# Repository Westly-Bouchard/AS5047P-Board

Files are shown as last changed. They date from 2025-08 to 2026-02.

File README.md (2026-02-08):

  Big thanks to [PCBWay](https://www.pcbway.com/) for sponsoring this project! Their support enables me (and hundreds of other designers) to make cool stuff. More info in [Manufacturing](#manufacturing)
<div align="center">
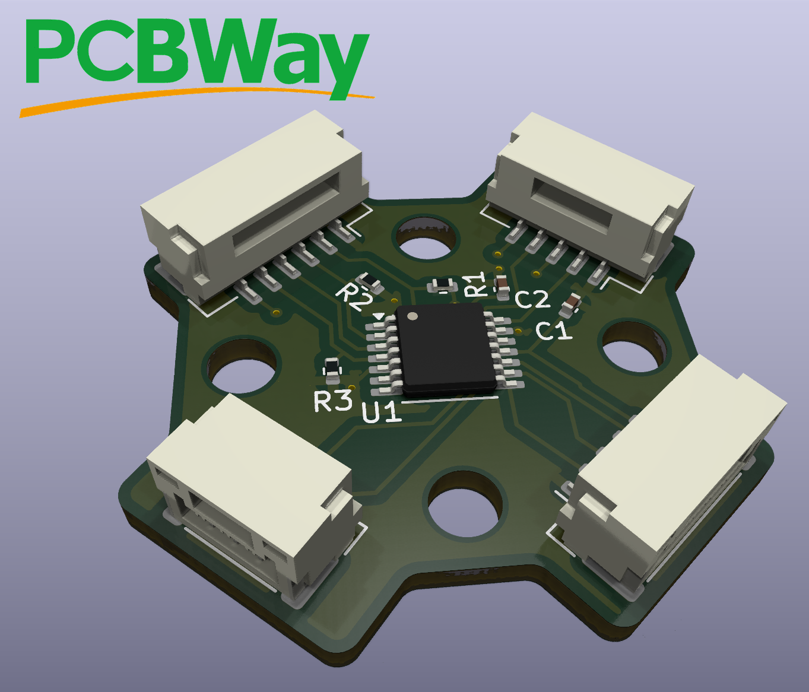
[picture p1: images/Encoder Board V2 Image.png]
  
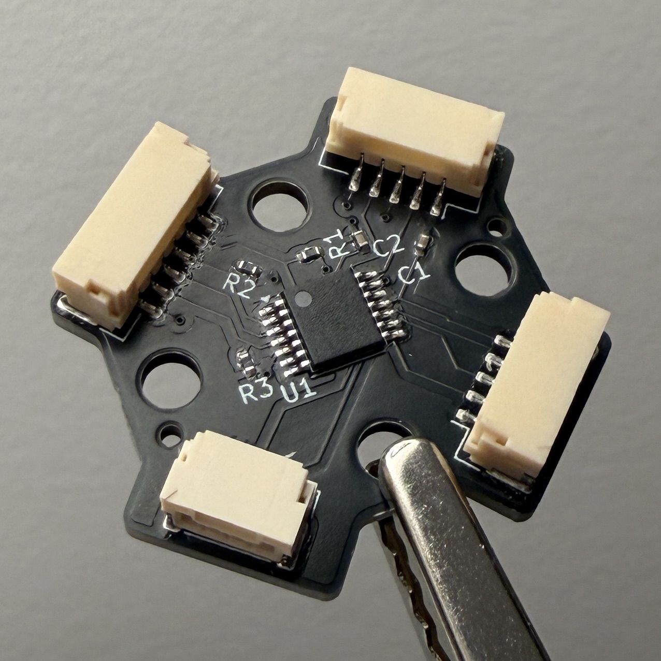
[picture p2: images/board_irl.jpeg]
  
</div>
<br>
<p>
This is a breakout pcb for the commonly used AS5047P magnetic position sensor IC. Its SPI communication protocols are supported by many motor drivers such as VESCs and ODrives (newer ODrives have them built in, but boards based on the older open source designs like the ODesc don't). I designed this in KiCad, so if you want to work on it you'll need to install that.

It's also designed to mount easily with generic 360kv 5010 brushless motors like [these](https://speedyfpv.com/collections/brushless-motors/products/5010-brushless-motor-360kv-2-6s-high-torque-motor-for-14-18-props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). The mounting hole placement is sketched in an image below. There are two sets of holes, the wider set are 19mm apart and the closer set are 16mm apart.

This board exposes all possible communication interfaces with the IC:
- SPI
- ABI
- UVW
- PWM

Although it should be noted that some of these modes may require additional configuration over SPI to work (I believe the UVW mode needs to know the number of poles on the motor to function properly). Refer to the [datasheet](https://look.ams-osram.com/m/d05ee39221f9857/original/AS5047P-DS000324.pdf) for more information.

This board allows for either 3.3 or 5 volt operation through a solder jumper on the back side, and all of the connectors are JST GH (kits for these are easily available on amazon).

## Manufacturing
All of the files needed to manufacture these boards are provided in the `fabrication` folder.

The process is super easy if you use PCBWay:
1. Upload the `gerber.zip` file to their [instant quote tool](https://www.pcbway.com/QuickOrderOnline.aspx)
    * The default quantity is 5pcs, if you want more, change that here
    * This is a great opportunity to pick a specific color if you want something other than green
    * You may also want to select the `HASL lead free` option rather than the default leaded one
2. You can get bare boards, but assembling them yourself can be a pain. Fortunately, PCBWay can assemble them for you!
    1. Check the `Assembly Service` box. The default options are fine here, make sure to set the quantity of boards you want assembled.
    2. You can now hit the `Save to Cart` button on the right hand side of the screen.
    3. You'll be taken to the orders page, where you'll have to upload a couple more files.
    4. Hit the `Add File` button and upload the `Bom.csv` and `Centroid.csv` files
    5. Now the engineers at PCBWay have to review the order to ensure that everything is correct
    6. Once this process is compete, you can check out, and production will start

PCBWay's amazing customer service team will email you with updates and to check things like component placement throughout the process. But, these boards are fairly simple and there should be no issues here. You can also check the exact status of your order at any time on the website.

> ✅ Results
> 
> I am certainly biased, but I've found that PCBWay is easily the best way to get PCBs made. The quality of the silkscreen and accuracy of component placement are great. And, the constant updates & communications from the PCBWay team give me great confidence that my projects will succeed on the first try.
>
> I highly recommend their services. And, by supporting them, you support small projects and independent designers like myself!
<hr>

When it's all said and done, these cost me about $10 per board with shipping and tariffs included (I live in the US). If you choose the cheaper shipping option and don't have to deal with crazy tariffs, then these could get down closer to $7 per board, which is a fantastic deal. Especially considering that similar encoders like the AS5048A on amazon cost closer to $14 per board (at least at the time of writing).

If you find a mistake, or want to make an improvement, feel free to open a pr!

Mounting hole spacing, the holes are M3.
</p>
<div align="center">
  Screenshot 2025-07-25 at 11 12 52 PM
</div>

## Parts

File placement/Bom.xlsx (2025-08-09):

Comment | Designator | Footprint | JLCPCB Part #
100nF | C1 | C_0402_1005Metric | C1525
1uF | C2 | C_0402_1005Metric | C52923
JST GH SM06 | J1 | JST_GH_SM06B-GHS-TB_1x06-1MP_P1.25mm_Horizontal | C133065
JST GH SM05 | J2,J3 | JST_GH_SM05B-GHS-TB_1x05-1MP_P1.25mm_Horizontal | C189896
JST GH SM03 | J4 | JST_GH_SM03B-GHS-TB_1x03-1MP_P1.25mm_Horizontal | C514175
AS5047P | U1 | Package_SO:TSSOP-14_4.4x5mm_P0.65mm | C962063
10kOhm | R1,R2,R3 | R_0402_1005Metric | C25744

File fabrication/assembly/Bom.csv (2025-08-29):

Item # | Designator | Quantity | Manufacturer | Mfg Part # | Description / Value | Package / Footprint | Notes
1 | J1 | 1 | JST | SM06B-GHS-TB(LF)(SN) |  | SMD,P=1.25mm,Surface Mount,Right Angle
2 | U1 | 1 | AMS | AS5047P-ATSM | AS5047P | TSSOP-14
3 | J4 | 1 | JST | SM03B-GHS-TB(LF)(SN) |  | SMD,P=1.25mm,Surface Mount,Right Angle
4 | R1,R2,R3 | 3 |  |  | 10k | 0402 | 10kOhm Resistor, 0402R
5 | J2,J3 | 2 | JST | SM05B-GHS-TB(LF)(SN) |  | SMD,P=1.25mm,Surface Mount,Right Angle
6 | C1 | 1 |  |  | 100nF | 0402 | 100nF Capacitor, 0402C
7 | C2 | 1 |  |  | 1uF | 0402 | 1uF Capacitor, 0402C

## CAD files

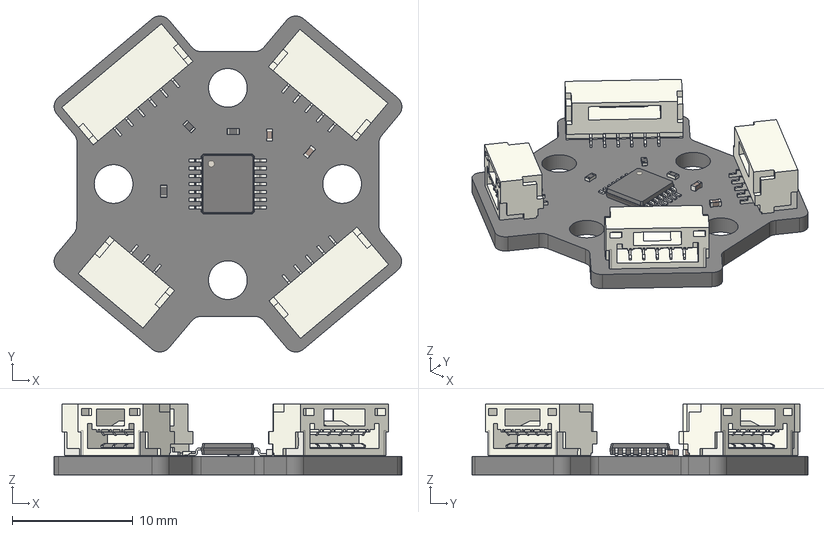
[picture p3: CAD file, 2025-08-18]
EncoderBoard.step
28.8 x 27.8 x 5.84 mm
JST_GH_SM06B-GHS-TB_1x06-1MP_P1.25mm_Horizontal
TSSOP-14_4.4x5mm_P0.65mm
JST_GH_SM03B-GHS-TB_1x03-1MP_P1.25mm_Horizontal
R_0402_1005Metric x 3
JST_GH_SM05B-GHS-TB_1x05-1MP_P1.25mm_Horizontal x 2
C_0402_1005Metric x 2
EncoderBoard_PCB

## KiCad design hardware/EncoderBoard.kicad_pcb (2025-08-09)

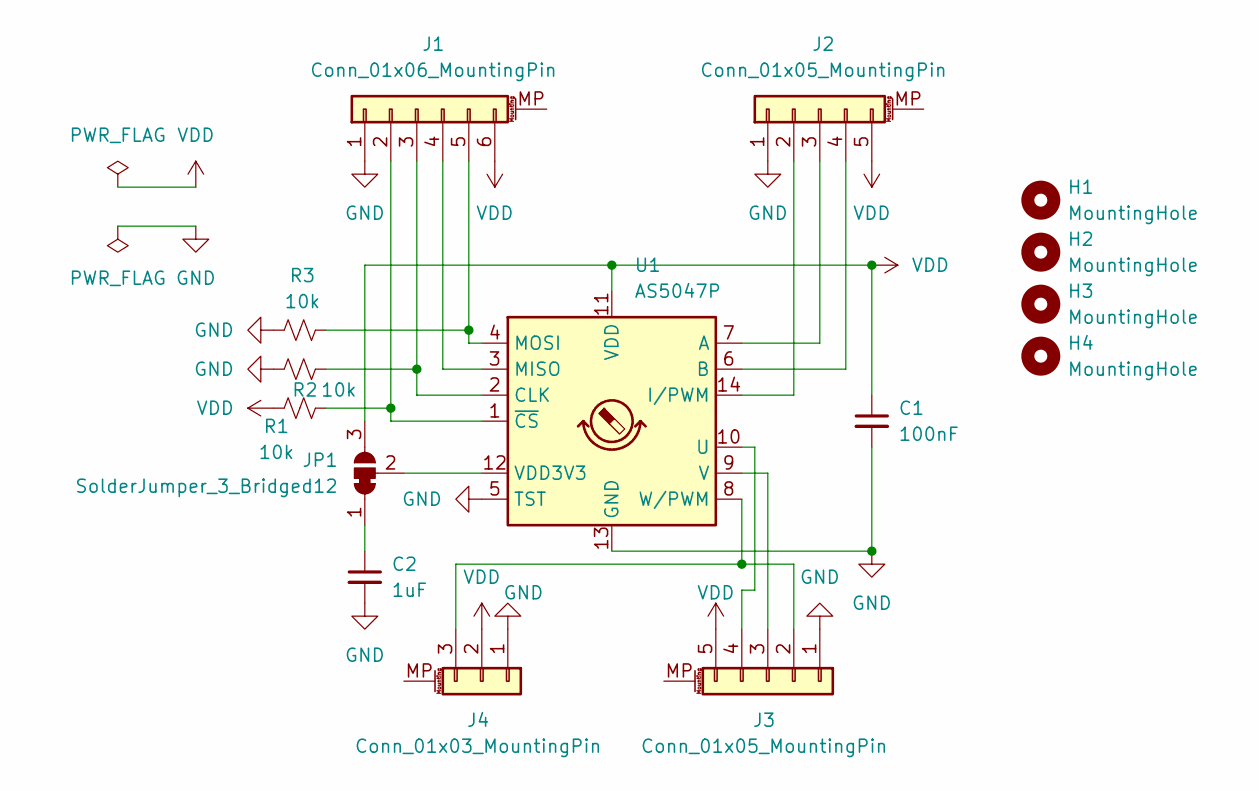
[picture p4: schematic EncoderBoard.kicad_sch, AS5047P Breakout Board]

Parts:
C1: 100nF; C_0402_1005Metric
C2: 1uF; C_0402_1005Metric
H1, H2, H3, H4: MountingHole; MountingHole_3.2mm_M3
J1: Conn_01x06_MountingPin; JST_GH_SM06B-GHS-TB_1x06-1MP_P1.25mm_Horizontal
J2, J3: Conn_01x05_MountingPin; JST_GH_SM05B-GHS-TB_1x05-1MP_P1.25mm_Horizontal
J4: Conn_01x03_MountingPin; JST_GH_SM03B-GHS-TB_1x03-1MP_P1.25mm_Horizontal
JP1: SolderJumper_3_Bridged12; SolderJumper-3_P1.3mm_Open_RoundedPad1.0x1.5mm
R1, R2, R3: 10k; R_0402_1005Metric
U1: AS5047P; TSSOP-14_4.4x5mm_P0.65mm

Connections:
GND: C1.2, C2.2, J1.1, J2.1, J3.1, J4.1, R2.1, R3.1, U1.5 (TST), U1.13 (GND)
unnamed: J1.2, R1.2, U1.1 (~CS)
unnamed: J1.3, R2.2, U1.2 (CLK)
unnamed: J1.4, U1.3 (MISO)
unnamed: J1.5, R3.2, U1.4 (MOSI)
unnamed: J2.2, U1.14 (I/PWM)
unnamed: J2.3, U1.7 (A)
unnamed: J2.4, U1.6 (B)
unnamed: J3.2, J4.3, U1.8 (W/PWM)
unnamed: J3.3, U1.9 (V)
unnamed: J3.4, U1.10 (U)
unnamed: C2.1, JP1.1 (A)
unnamed: JP1.2 (C), U1.12 (VDD3V3)
VDD: C1.1, J1.6, J2.5, J3.5, J4.2, JP1.3 (B), R1.1, U1.11 (VDD)

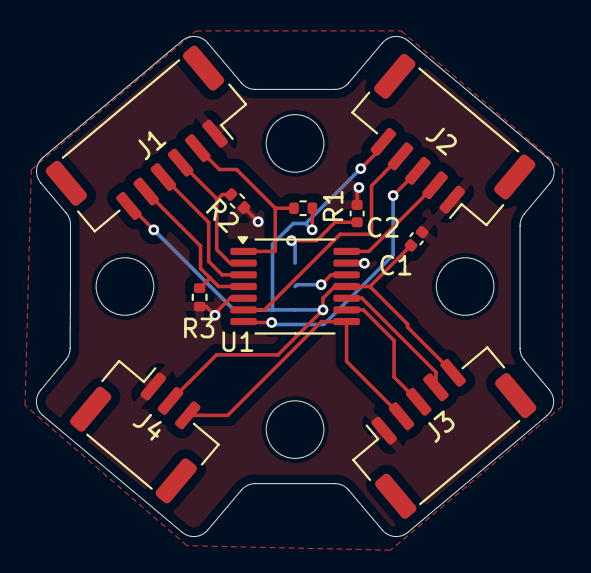
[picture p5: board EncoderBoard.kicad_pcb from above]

Board: 2 copper layers, 28.8 x 27.8 mm, 15 parts (1 on the bottom side), 14 nets.

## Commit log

2025-08-09 Update for V2
    [Bom.xlsx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]
2025-08-18 Add step file
    [EncoderBoard.step]
2025-08-22 Remove more stuff
    [EncoderBoard.csv, EncoderBoard.kicad_pcb, EncoderBoard.kicad_sch]
2025-08-23 Add fabrication files
    [Bom.csv, Bom.xlsx, Centroid.csv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]
2025-12-21 Update with PCBWay shout-out
